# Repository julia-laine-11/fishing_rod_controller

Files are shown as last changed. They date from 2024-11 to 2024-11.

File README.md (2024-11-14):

# fishing_rod_controller
This was part of an EPICS team project for an automatically casting and reeling fishing rod. I designed this PCB for the controller so it would stop falling apart during travel and use.

Our project partner was a [kid named Colton in Indianapolis](https://www.facebook.com/ColtonsQuest/) who has AMC. He likes to fish but he cannot hold the fishing rod. Our team designed an automatically casting and reeling fishing rod to help him out.

I took lead of the electronics on the team and I created this PCB:



*top view*



*bottom view*



*schematic*

## Pictures of use and design:




*the initial design tested on a breadboard*

 

*the first PCB design - I forgot to add thru holes to connect the ground planes*

 

*the second PCB design. I made more changes as I learned from my first design. Notice the larger isolation and more options for alternate parts.*



*my teammates on the left, our project partner, Colton, on the right*

[Here is a video](https://www.facebook.com/reel/425838616804608) of Colton using it.

[And another](https://www.facebook.com/share/v/JBNppNtS4n77EEXA/)



*Colton and a fish he caught with the fishing rod*



*our team and Colton*

## Controller housing



*The lid is seperate and there are 3 buttons on the top. The controller housing is a triangle shape so Colton can easily hold it between his legs.*

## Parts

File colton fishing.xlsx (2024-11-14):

Country of Origin may be different at time of shipment.
The HTSUS and ECCN information shown is for informational purposes only and is not a representation or warranty as to the accuracy or reliability of these classifications. All information is provided "as is" and is subject to change without notice. Any use made of the information provided is without recourse to Digi-Key and at the user's risk.
Index | Manufacturer Part Number | Manufacturer Name | Description | Availability | Stock Status | Attrition % | Requested Quantity 1 | Pack Quantity 1 | Pack Type 1 | Digi-Key Part Number 1 | Unit Price 1 | Extended Price 1 | Minimum Order Quantity 1 | Customer Reference | Requested Part Number | Lead Weeks | Datasheet | Reference Designator | US Import Tariff | Note | Part Status | RoHS Status | Moisture Sensitivity Level (MSL) | ECCN | HTSUS | Country of Origin | Environmental Information | Original Part numbers | Image
1 | 282837-2 | TE Connectivity AMP Connectors | TERM BLK 2P SIDE ENT 5.08MM PCB | 134,618 | In Stock |  | 5 | 5 | Bulk | A113320-ND | 0.70000 | $3.50 | 1 |  | 282837-2 | 44 | https://www.te.com/usa-en/product-282837-2.datasheet.pdf |  | N/A |  | Active | ROHS3 Compliant | 1 (Unlimited) | EAR99 | 8536.90.4000 | Italy | http://www.te.com/commerce/alt/SinglePartSearch.do?PN=282837-2&dest=stmt | 282837-2 | https://mm.digikey.com/Volume0/opasdata/d220001/medias/images/1207/282837-2.JPG
2 | 282837-3 | TE Connectivity AMP Connectors | TERM BLK 3P SIDE ENT 5.08MM PCB | 230,570 | In Stock |  | 2 | 2 | Bulk | A113321-ND | 0.97000 | $1.94 | 1 |  | 282837-3 | 32 | https://www.te.com/usa-en/product-282837-3.datasheet.pdf |  | N/A |  | Active | ROHS3 Compliant | 1 (Unlimited) | EAR99 | 8536.90.4000 | Italy | http://www.te.com/commerce/alt/SinglePartSearch.do?PN=282837-3&dest=stmt | 282837-3 | https://mm.digikey.com/Volume0/opasdata/d220001/medias/images/1027/282837-3.JPG
3 | NE555DR | Texas Instruments | IC OSC SGL TIMER 100KHZ 8-SOIC | 305,542 | In Stock |  | 1 | 1 | Cut Tape (CT) | 296-6501-1-ND | 0.47000 | $0.47 | 1 |  | 296-6501-1-ND | 6 | https://www.ti.com/general/docs/suppproductinfo.tsp?distId=10 |  | N/A |  | Active | ROHS3 Compliant | 1 (Unlimited) | EAR99 | 8542.39.0001 | Malaysia |  | 296-6501-1-ND | https://mm.digikey.com/Volume0/opasdata/d220001/medias/images/4849/296_8-SOIC.jpg
4 | CR0603-JW-224ELF | Bourns Inc. | RES SMD 220K OHM 5% 1/10W 0603 | 19,554 | In Stock |  | 1 | 1 | Cut Tape (CT) | CR0603-JW-224ELFCT-ND | 0.10000 | $0.10 | 1 |  | CR0603-JW-224ELFCT-ND | 15 | https://www.bourns.com/docs/product-datasheets/cr.pdf?sfvrsn=574d41f6_14 |  | N/A |  | Active | ROHS3 Compliant | 1 (Unlimited) | EAR99 | 8533.21.0030 | Taiwan | https://www.bourns.com/docs/rohs-content/bourns-reach-letter.pdf|https://www.bourns.com/docs/Product-MDS/cr0603_mds.pdf|https://www.bourns.com/docs/rohs-cofc/crx_coc.pdf?sfvrsn=db3a74f6_10 | CR0603-JW-224ELFCT-ND | https://mm.digikey.com/Volume0/opasdata/d220001/medias/images/505/CR0603-(1608-Metric).jpg
5 | CR0603-FX-5602ELF | Bourns Inc. | RES SMD 56K OHM 1% 1/10W 0603 | 113,169 | In Stock |  | 1 | 1 | Cut Tape (CT) | CR0603-FX-5602ELFCT-ND | 0.10000 | $0.10 | 1 |  | CR0603-FX-5602ELFCT-ND | 15 | https://www.bourns.com/docs/product-datasheets/cr.pdf?sfvrsn=574d41f6_14 |  | N/A |  | Active | ROHS3 Compliant | 1 (Unlimited) | EAR99 | 8533.21.0030 | Taiwan | https://www.bourns.com/docs/rohs-content/bourns-reach-letter.pdf|https://www.bourns.com/docs/Product-MDS/cr0603_mds.pdf|https://www.bourns.com/docs/rohs-cofc/crx_coc.pdf?sfvrsn=db3a74f6_10 | CR0603-FX-5602ELFCT-ND | https://mm.digikey.com/Volume0/opasdata/d220001/medias/images/505/CR0603-(1608-Metric).jpg
note: you will also need diodes (1n4148 and 1n4001)
these diodes are not on the list since they are available at EPICS

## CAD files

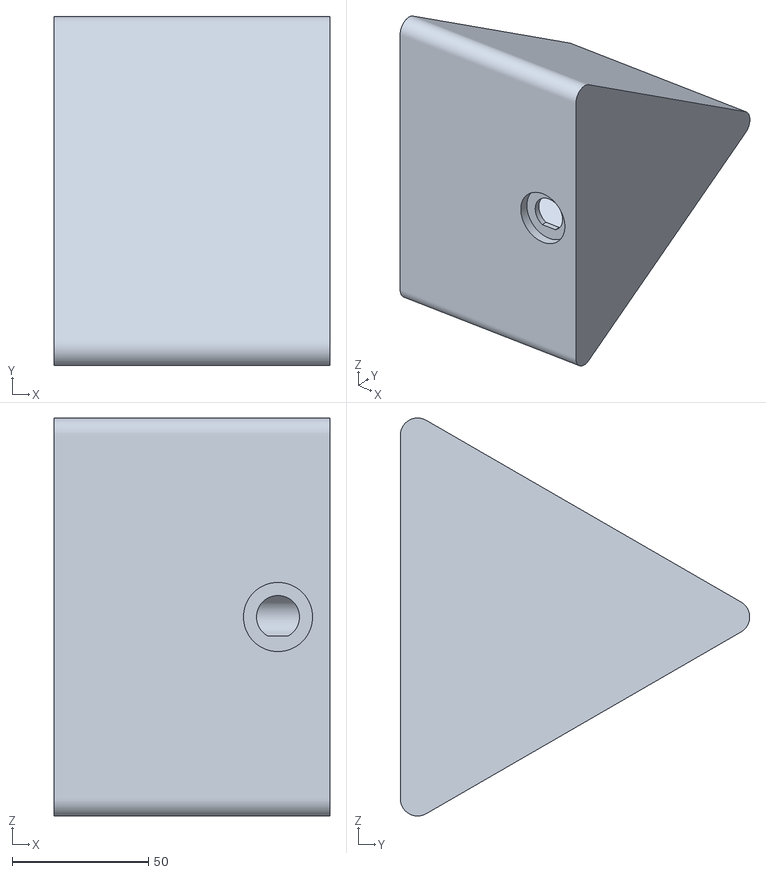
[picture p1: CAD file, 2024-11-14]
RemoteController_Base(2) (1).stl
101.3 x 128.4 x 146.3

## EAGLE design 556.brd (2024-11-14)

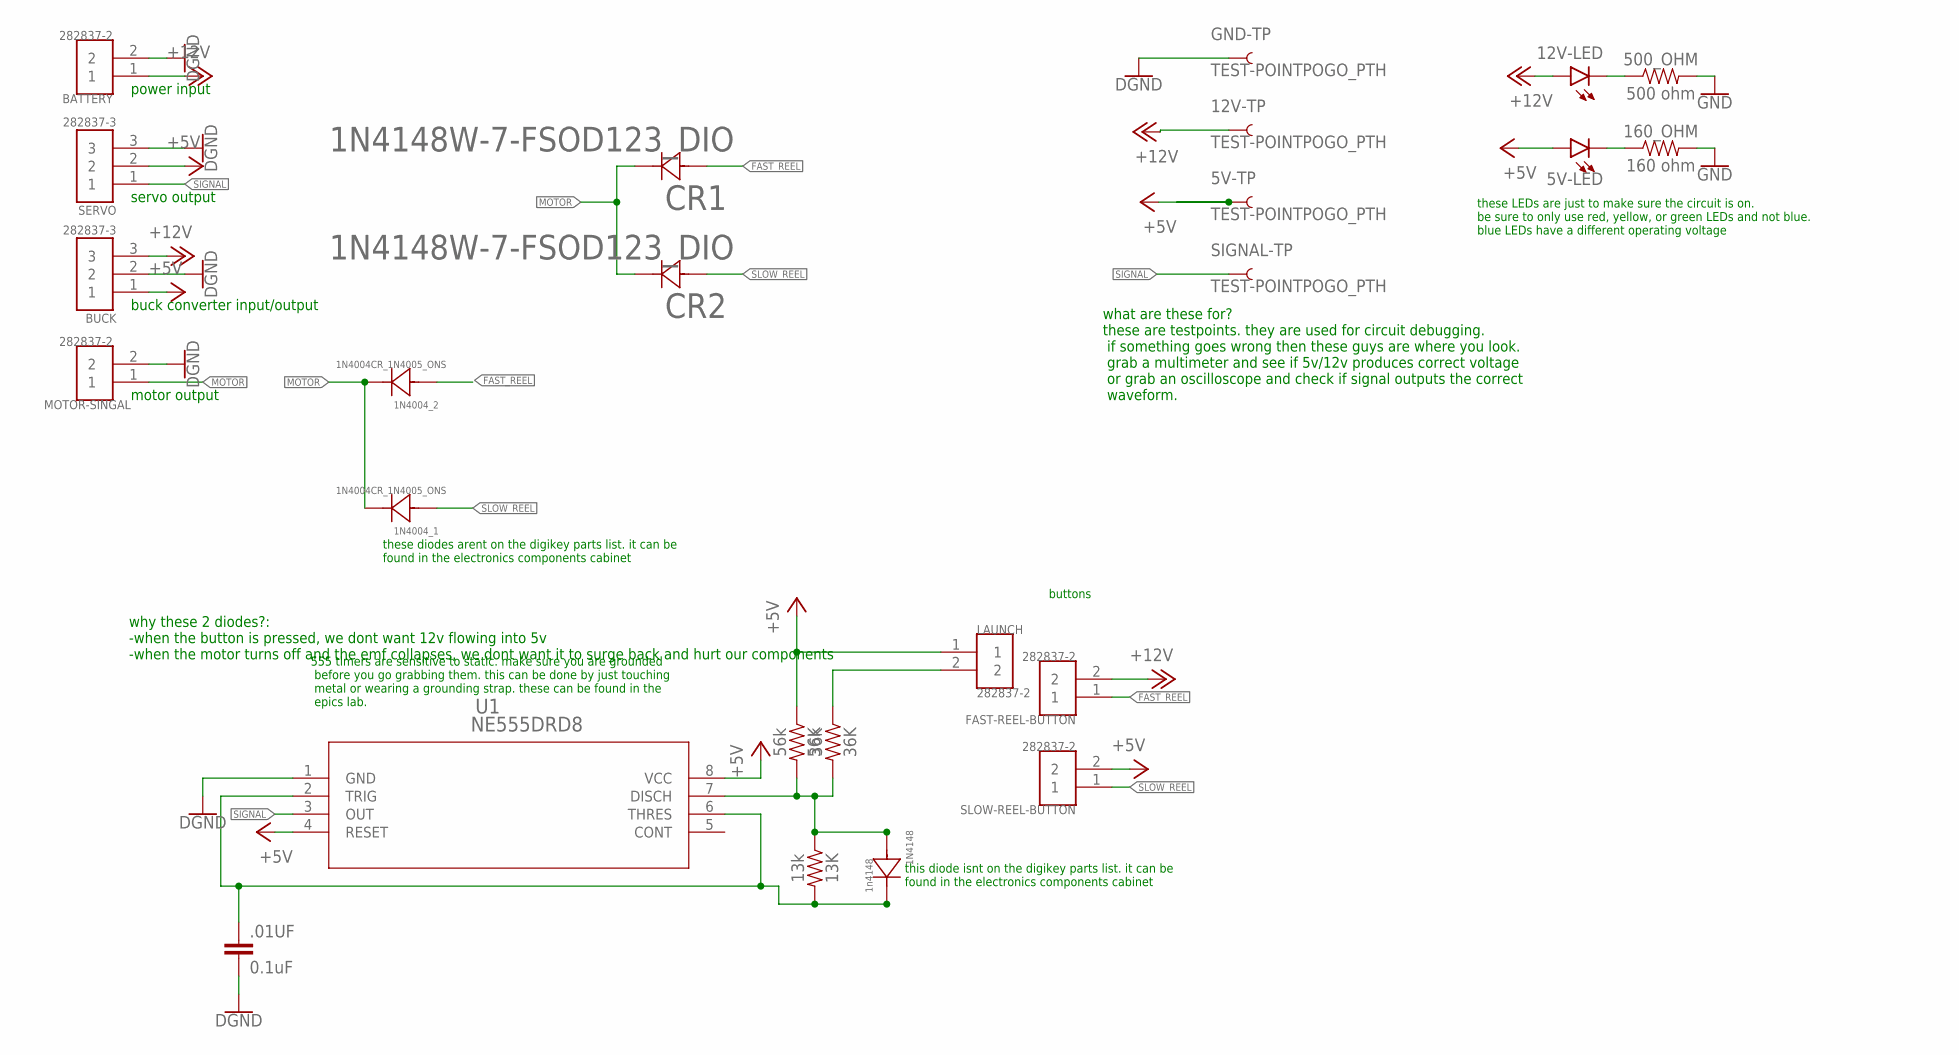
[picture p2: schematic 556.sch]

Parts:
1N4004_1, 1N4004_2: 1N4004CR_1N4005_ONS; CR_1N4005_ONS
1N4148: 1n4148; CR_1N4005_ONS
5V-LED, 12V-LED: LED0603; LED-0603
5V-TP, 12V-TP: TEST-POINTPOGO_PTH; 1X01_NO_SILK
13K: 13k; 0603
36K: 36k; 0603
56K: 56k; 0603
160_OHM: 160 ohm; 0603
500_OHM: 500 ohm; 0603
.01UF: 0.1uF; 0402-CAP
BATTERY: 282837-2; TE_282837-2
BUCK: 282837-3; TE_282837-3
CR1, CR2: 1N4148W-7-FSOD123_DIO; SOD123_DIO
FAST-REEL-BUTTON: 282837-2; TE_282837-2
GND-TP: TEST-POINTPOGO_PTH; 1X01_NO_SILK
LAUNCH: 282837-2; TE_282837-2
MOTOR-SINGAL: 282837-2; TE_282837-2
SERVO: 282837-3; TE_282837-3
SIGNAL-TP: TEST-POINTPOGO_PTH; 1X01_NO_SILK
SLOW-REEL-BUTTON: 282837-2; TE_282837-2
U1: NE555DRD8; D8

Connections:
+5V: 5V-LED.A, 5V-TP.1, 56K.1, BUCK.1, LAUNCH.1, SERVO.2, SLOW-REEL-BUTTON.2, U1.4 (RESET), U1.8 (VCC)
+12V: 12V-LED.A, 12V-TP.1, BATTERY.1, BUCK.3, FAST-REEL-BUTTON.2
FAST_REEL: 1N4004_2.2, CR1.2, FAST-REEL-BUTTON.1
GND: 160_OHM.2, 500_OHM.2, .01UF.2, BATTERY.2, BUCK.2, GND-TP.1, MOTOR-SINGAL.2, SERVO.3, U1.1 (GND)
MOTOR: 1N4004_1.1, 1N4004_2.1, CR1.1, CR2.1, MOTOR-SINGAL.1
unnamed: 36K.1, LAUNCH.2
unnamed: 1N4148.1, 13K.2, .01UF.1, U1.2 (TRIG), U1.6 (THRES)
unnamed: 1N4148.2, 13K.1, 36K.2, 56K.2, U1.7 (DISCH)
unnamed: 5V-LED.C, 160_OHM.1
unnamed: 12V-LED.C, 500_OHM.1
SIGNAL: SERVO.1, SIGNAL-TP.1, U1.3 (OUT)
SLOW_REEL: 1N4004_1.2, CR2.2, SLOW-REEL-BUTTON.1

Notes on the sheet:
why these 2 diodes?: -when the button is pressed, we dont want 12v flowing into 5v -when the motor turns off and the emf collapses, we dont want it to surge back and hurt our components
power input
servo output
buck converter input/output
motor output
what are these for? these are testpoints. they are used for circuit debugging. if something goes wrong then these guys are where you look. grab a multimeter and see if 5v/12v produces correct voltage or grab an oscilloscope and check if signal outputs the correct waveform.
these LEDs are just to make sure the circuit is on. be sure to only use red, yellow, or green LEDs and not blue. blue LEDs have a different operating voltage
555 timers are sensitive to static. make sure you are grounded before you go grabbing them. this can be done by just touching metal or wearing a grounding strap. these can be found in the epics lab.
this diode isnt on the digikey parts list. it can be found in the electronics components cabinet
these diodes arent on the digikey parts list. it can be found in the electronics components cabinet
buttons

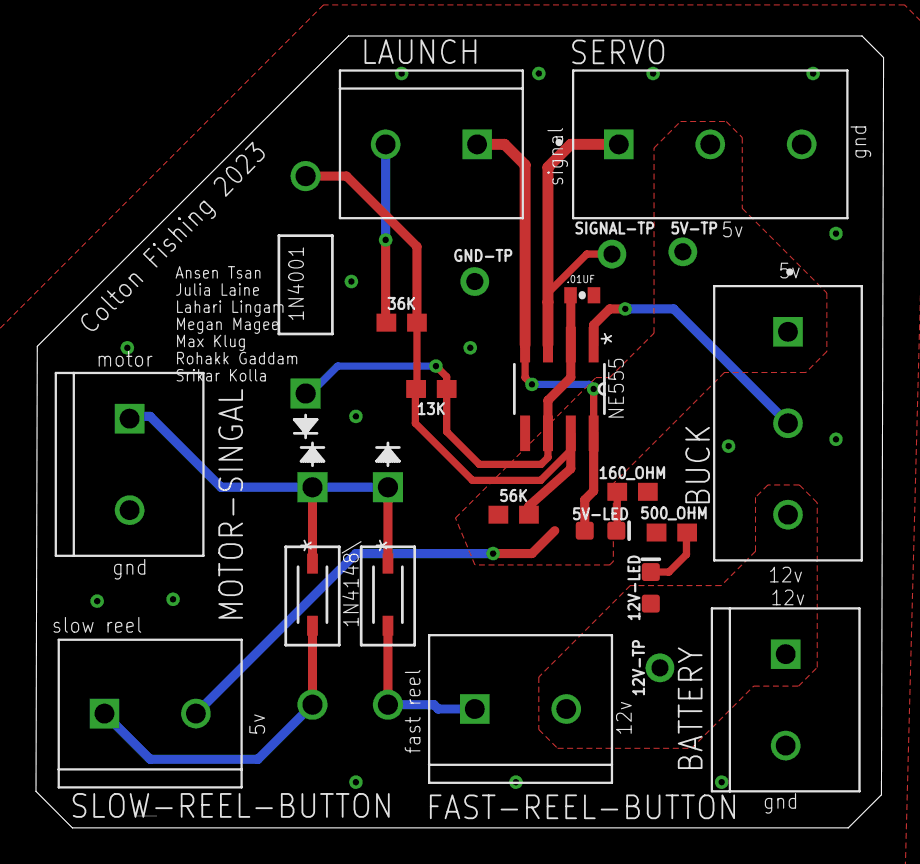
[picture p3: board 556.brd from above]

Board: 2 copper layers, 47.1 x 44.0 mm, 25 parts (0 on the bottom side), 12 nets.

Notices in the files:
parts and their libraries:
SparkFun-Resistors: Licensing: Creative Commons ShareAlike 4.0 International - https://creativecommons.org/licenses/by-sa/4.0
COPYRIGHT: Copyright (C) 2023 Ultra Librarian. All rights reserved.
